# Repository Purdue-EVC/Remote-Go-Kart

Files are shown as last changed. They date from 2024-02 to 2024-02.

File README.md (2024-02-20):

# Rc Go Kart
The Purdue EVC Club's code for the Rc Go kart.
## Setup
Currently using a red line 775 for the steering motor with a SparkMini as the motor controller.
Then using a Rev Robotics Through Bore Encoder for the steering shaft's positioning.
For the brakes we use a linear actuator with a potentiometer as the position sensor.
For motor control we use a sevcon gen4 size 4 with an unknown decade old brushless dc motor.
There is an stm32 controlling the entire kart.
For the remote controller we use a FlySky ia10b receiver with a FlySky i6X for the transmitter.
## Power
Power for all devices except the main motor is entirely from battery power passed through a 48v-12v/5v dc to dc converter. 
12v is supplied to the front steering, braking and the stm32. 5v is supplied to all other devices on the kart.
For the sevcon we use a keyed ignition start along with 2 estops in series connected to the contactor for the sevcon.
Battery power is supplied directly to the sevcon through the contactor.

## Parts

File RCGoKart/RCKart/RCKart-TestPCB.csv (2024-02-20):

Source: | /Users/ryan/Documents/GitHub/EVC-Remote-Cart/RCGoKart/RCKart/RCKart-TestPCB.kicad_sch
Date: | 2023 October 25, Wednesday 09:54:53
Tool: | Eeschema 7.0.7
Generator: | /Applications/KiCad/KiCad.app/Contents/SharedSupport/plugins/bom_csv_grouped_by_value.py
Component Count: | 9
Collated Components:
Item | Qty | Reference(s) | Value | LibPart | Footprint | Datasheet | DNP
1 | 1 | A1 | STM32 Nucleo Board | MCU_Module:Arduino_UNO_R3 | Module:Arduino_UNO_R3_Bare | https://www.arduino.cc/en/Main/arduinoBoardUno
2 | 1 | J1 | Throttle | Connector_Generic:Conn_01x01 | Connector_PinSocket_2.54mm:PinSocket_1x01_P2.54mm_Vertical | ~
3 | 1 | J2 | Brake Controller | Connector_Generic:Conn_01x02 | Connector_PinSocket_2.54mm:PinSocket_1x02_P2.54mm_Vertical | ~
4 | 2 | J3, J13 | RC Channels | Connector_Generic:Conn_01x10 | Connector_PinSocket_2.54mm:PinSocket_1x10_P2.54mm_Vertical | ~
5 | 1 | J6 | Power | Connector:Screw_Terminal_01x03 | TerminalBlock:TerminalBlock_bornier-3_P5.08mm | ~
6 | 1 | J9 | SIG | Connector:Conn_01x04_Socket | Connector_PinSocket_2.54mm:PinSocket_1x04_P2.54mm_Vertical | ~
7 | 1 | J10 | PWR | Connector:Conn_01x04_Socket | Connector_PinSocket_2.54mm:PinSocket_1x04_P2.54mm_Vertical | ~
8 | 1 | J11 | GND | Connector:Conn_01x04_Socket | Connector_PinSocket_2.54mm:PinSocket_1x04_P2.54mm_Vertical | ~

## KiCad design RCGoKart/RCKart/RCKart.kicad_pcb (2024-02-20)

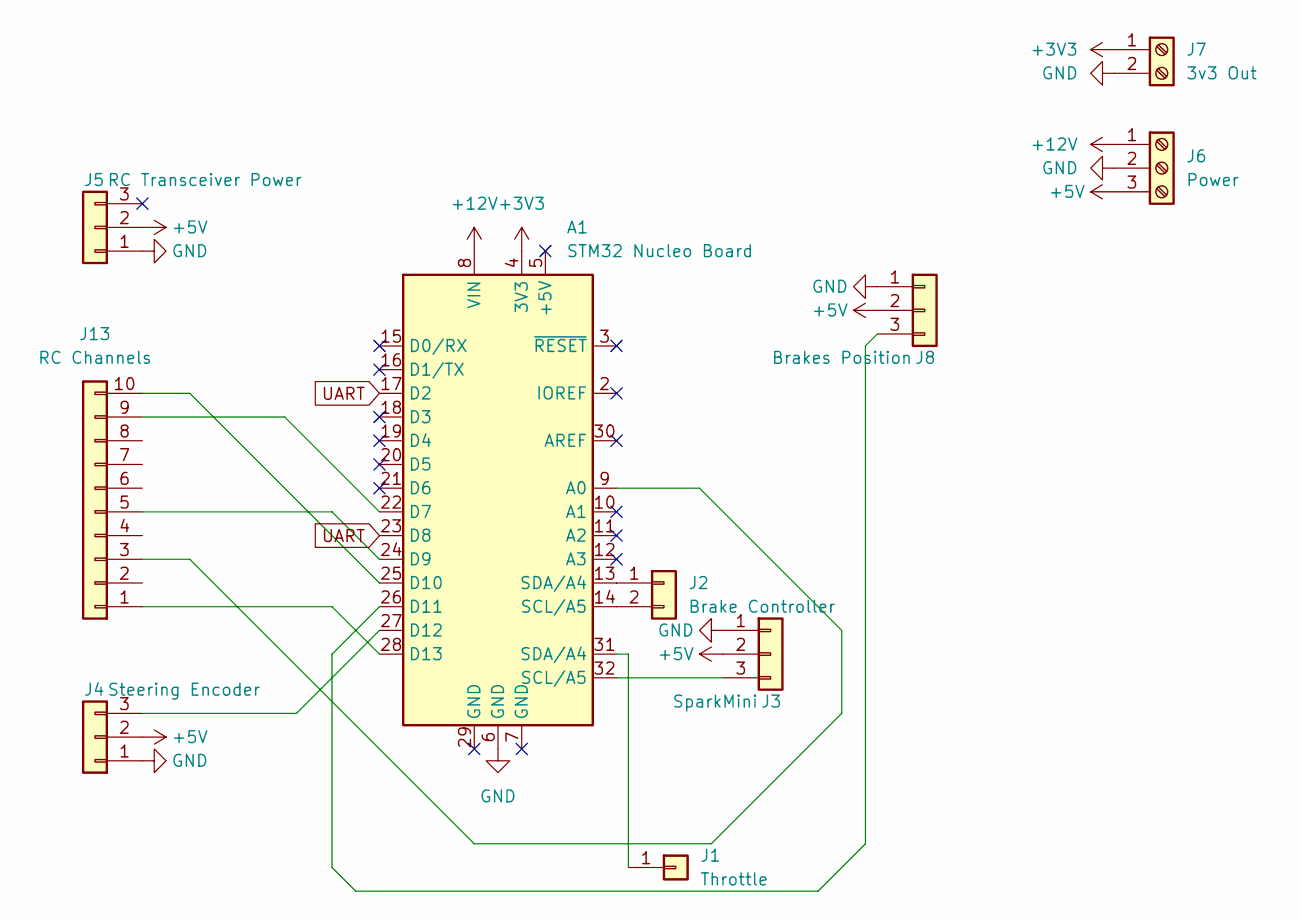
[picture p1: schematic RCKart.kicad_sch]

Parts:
A1: STM32 Nucleo Board; Arduino_UNO_R3_Bare
J1: Throttle; PinSocket_1x01_P2.54mm_Vertical
J2: Brake Controller; PinSocket_1x02_P2.54mm_Vertical
J3: SparkMini; PinHeader_1x03_P2.54mm_Vertical
J4: Steering Encoder; PinHeader_1x03_P2.54mm_Vertical
J5: RC Transceiver Power; PinSocket_1x03_P2.54mm_Vertical
J6: Power; TerminalBlock_bornier-3_P5.08mm
J7: 3v3 Out; TerminalBlock_bornier-2_P5.08mm
J8: Brakes Position; PinSocket_1x03_P2.54mm_Vertical
J13: RC Channels; PinSocket_1x10_P2.54mm_Vertical

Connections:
+3V3: A1.4 (3V3), J7.1
+5V: J3.2, J4.2, J5.2, J6.3, J8.2
+12V: A1.8 (VIN), J6.1
GND: A1.6 (GND), J3.1, J4.1, J5.1, J6.2, J7.2, J8.1
unnamed: A1.9 (A0), J13.3
unnamed: A1.22 (D7), J13.9
unnamed: A1.24 (D9), J13.5
unnamed: A1.25 (D10), J13.10
unnamed: A1.26 (D11), J8.3
unnamed: A1.27 (D12), J4.3
unnamed: A1.28 (D13), J13.1
unnamed: A1.31 (SDA/A4), J1.1
unnamed: A1.13 (SDA/A4), J2.1
unnamed: A1.14 (SCL/A5), J2.2
unnamed: A1.32 (SCL/A5), J3.3
UART: A1.17 (D2), A1.23 (D8)

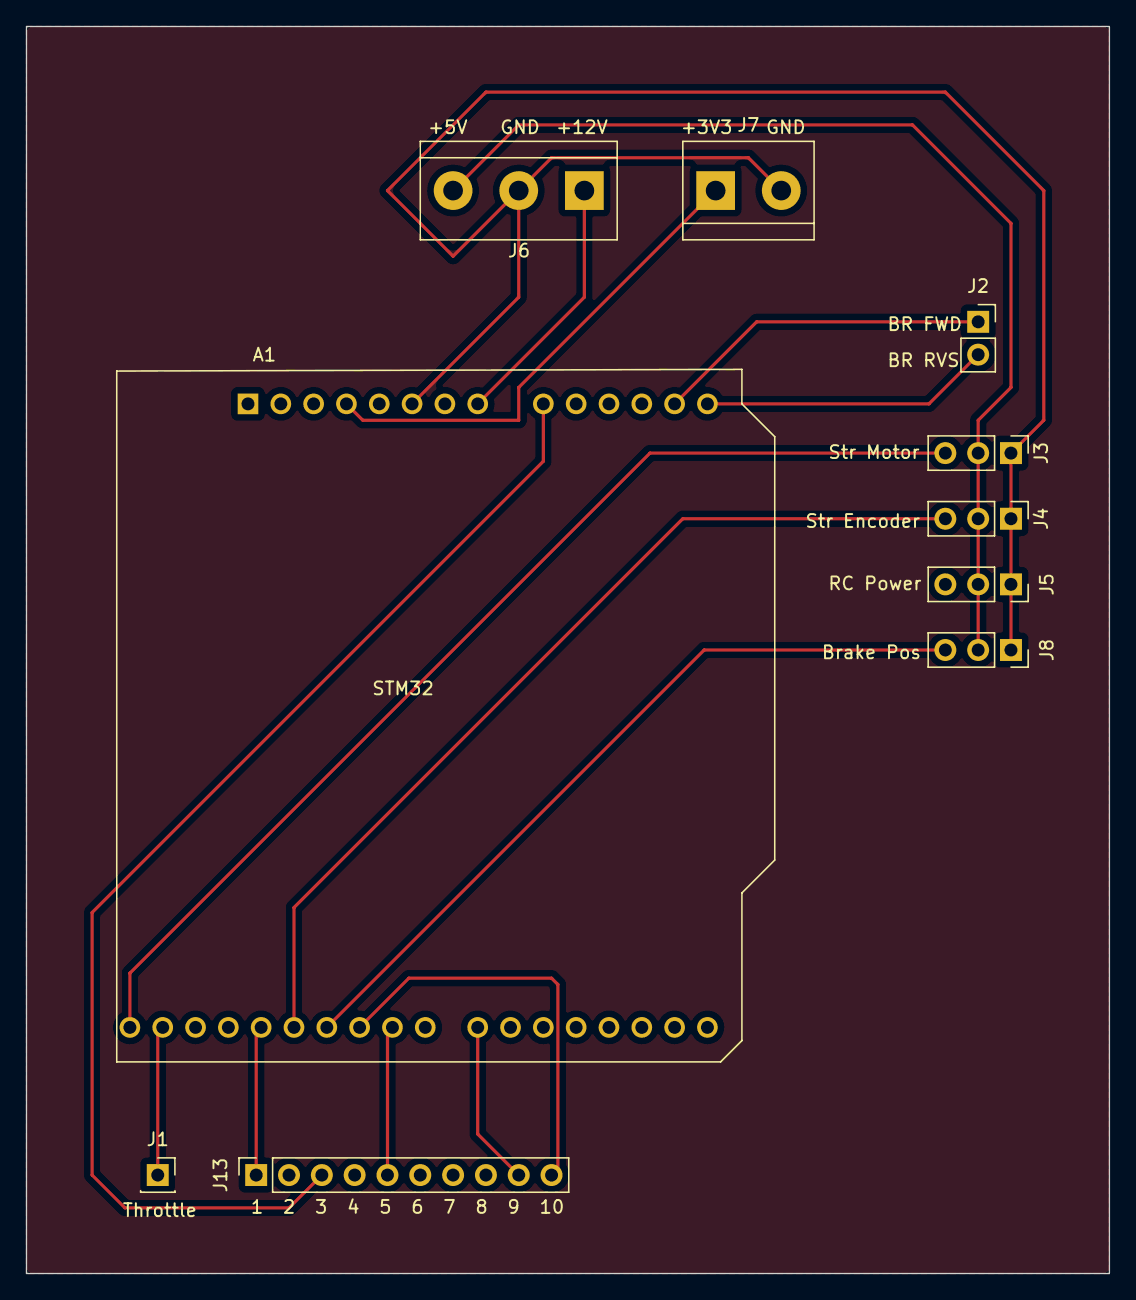
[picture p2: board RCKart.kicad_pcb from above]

Board: 2 copper layers, 83.8 x 96.5 mm, 10 parts (0 on the bottom side), 16 nets.

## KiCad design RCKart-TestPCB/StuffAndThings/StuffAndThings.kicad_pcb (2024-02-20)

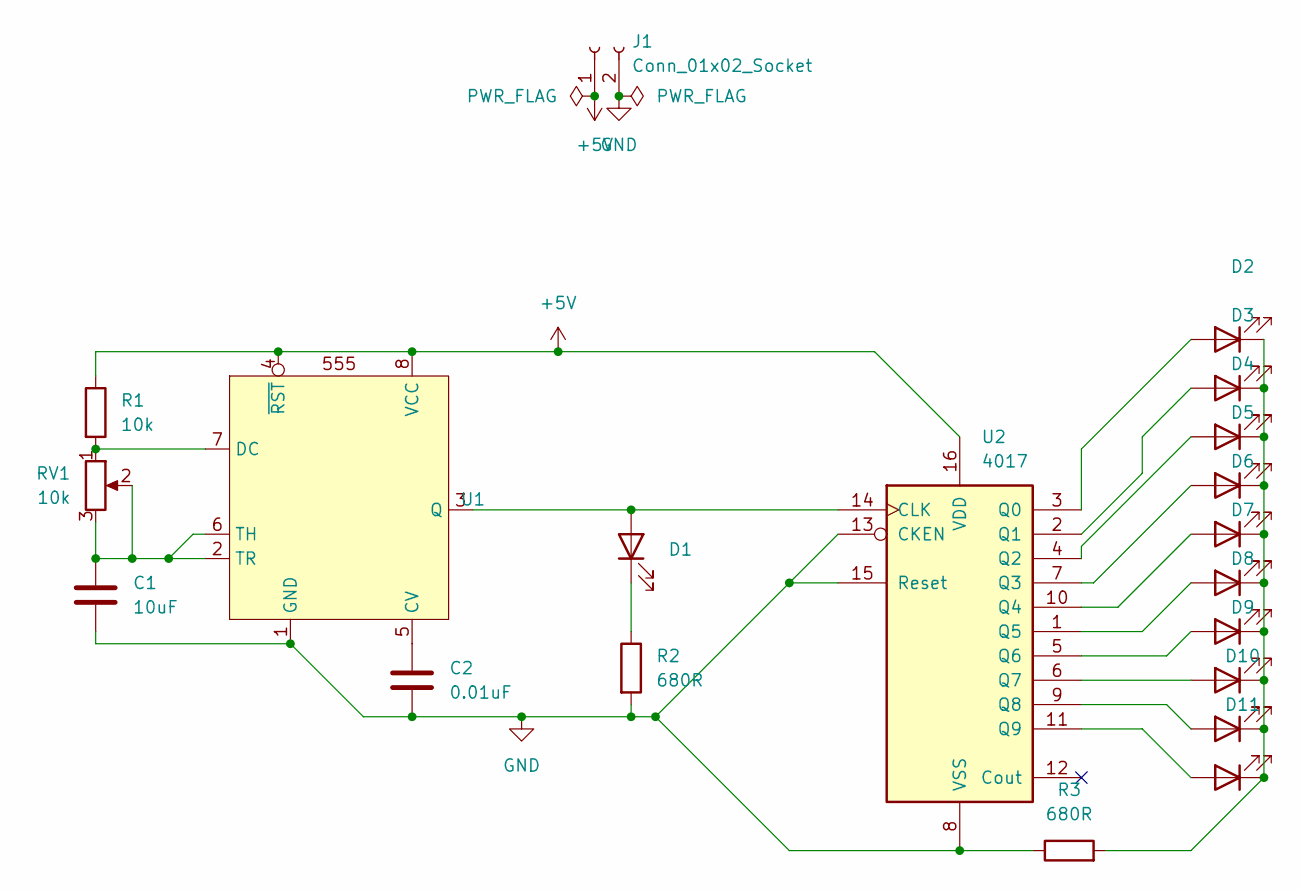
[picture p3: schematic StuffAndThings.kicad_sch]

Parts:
C1: 10uF; C_0402_1005Metric
C2: 0.01uF; C_0402_1005Metric
D1, D2, D3, D4, D5, D6, D7, D8, D9, D10, D11: D_0402_1005Metric
J1: Conn_01x02_Socket; PinSocket_1x02_P2.54mm_Vertical
R1: 10k; R_0402_1005Metric
R2: 680R; R_0603_1608Metric
R3: 680R; R_0402_1005Metric
RV1: 10k; Potentiometer_Bourns_3269P_Horizontal
U1: SOIC-8_3.9x4.9mm_P1.27mm
U2: 4017; SOIC-16_3.9x9.9mm_P1.27mm

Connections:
+5V: J1.1, R1.1, U1.4 (~RST), U1.8 (VCC), U2.16 (VDD)
GND: C1.2, C2.2, J1.2, R2.2, R3.1, U1.1 (GND), U2.8 (VSS), U2.13 (CKEN), U2.15 (Reset)
unnamed: D1.2 (A), U1.3 (Q), U2.14 (CLK)
unnamed: D1.1 (K), R2.1
unnamed: D2.2 (A), U2.3 (Q0)
unnamed: D3.2 (A), U2.2 (Q1)
unnamed: D4.2 (A), U2.4 (Q2)
unnamed: D5.2 (A), U2.7 (Q3)
unnamed: D6.2 (A), U2.10 (Q4)
unnamed: D7.2 (A), U2.1 (Q5)
unnamed: D8.2 (A), U2.5 (Q6)
unnamed: D9.2 (A), U2.6 (Q7)
unnamed: D10.2 (A), U2.9 (Q8)
unnamed: D2.1 (K), D3.1 (K), D4.1 (K), D5.1 (K), D6.1 (K), D7.1 (K), D8.1 (K), D9.1 (K), D10.1 (K), D11.1 (K), R3.2
unnamed: D11.2 (A), U2.11 (Q9)
unnamed: C2.1, U1.5 (CV)
unnamed: R1.2, RV1.1, U1.7 (DC)
unnamed: C1.1, RV1.2, RV1.3, U1.2 (TR), U1.6 (TH)

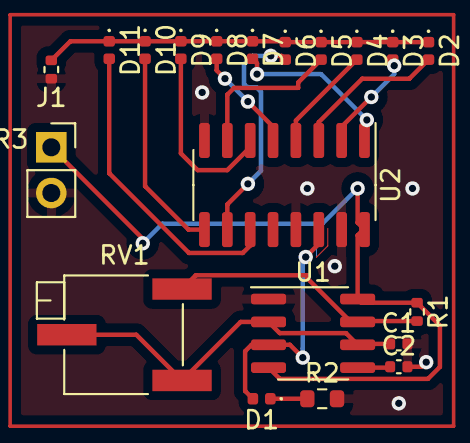
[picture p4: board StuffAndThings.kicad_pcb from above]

Board: 2 copper layers, 20 parts (0 on the bottom side), 18 nets.

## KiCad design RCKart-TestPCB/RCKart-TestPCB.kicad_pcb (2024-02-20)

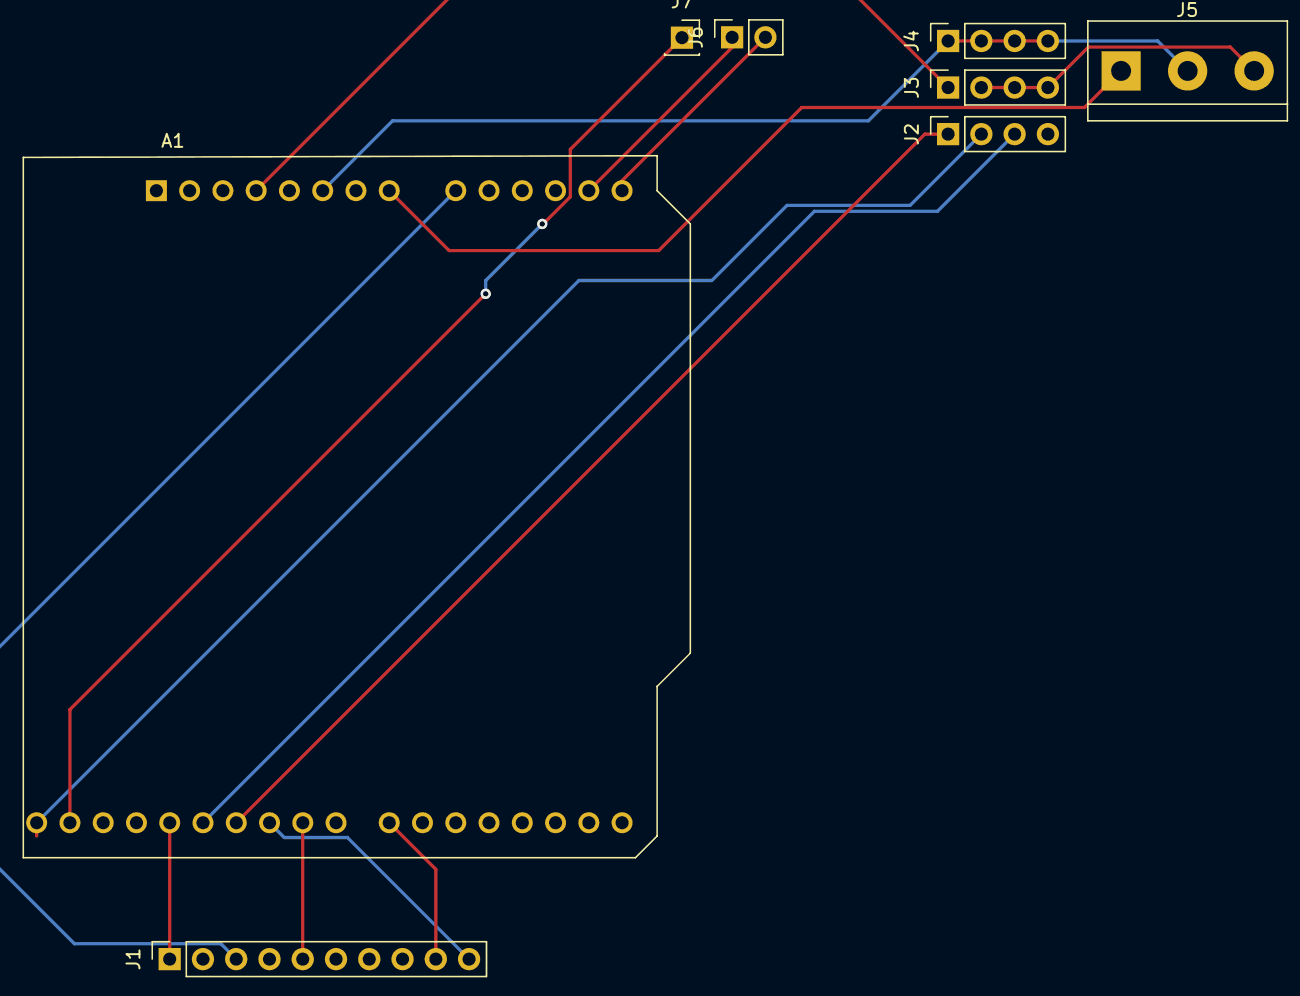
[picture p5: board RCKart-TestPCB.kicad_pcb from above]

Board: 2 copper layers, 8 parts (0 on the bottom side), 15 nets.

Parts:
A1: STM32 Nucleo Board; Arduino_UNO_R3_Bare
J1: RC Channels; PinSocket_1x10_P2.54mm_Vertical
J2: SIG; PinSocket_1x04_P2.54mm_Vertical
J3: PWR; PinSocket_1x04_P2.54mm_Vertical
J4: GND; PinSocket_1x04_P2.54mm_Vertical
J5: Power; TerminalBlock_bornier-3_P5.08mm
J6: Brake Controller; PinSocket_1x02_P2.54mm_Vertical
J7: Throttle; PinSocket_1x01_P2.54mm_Vertical

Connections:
+3V3: A1.4 (3V3), J3.1
+5V: J3.2, J3.3, J3.4, J5.3
+12V: A1.8 (VIN), J5.1
BP: A1.26 (D11), J2.1
ESTOP: A1.25 (D10), J1.10
GND: A1.6 (GND), J4.1, J4.2, J4.3, J4.4, J5.2
MAX SPD: A1.24 (D9), J1.5
unnamed: A1.13 (SDA/A4), J6.1
unnamed: A1.14 (SCL/A5), J6.2
unnamed: A1.31 (SDA/A4), J7.1
SM: A1.32 (SCL/A5), J2.2
STATE: A1.22 (D7), J1.9
STR ENC: A1.27 (D12), J2.3
STR IN: A1.28 (D13), J1.1
THR IN: A1.9 (A0), J1.3

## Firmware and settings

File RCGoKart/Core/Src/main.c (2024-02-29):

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
/* Includes ------------------------------------------------------------------*/
#include "main.h"

/* USER CODE BEGIN Includes */
#include <stdio.h>
#include <stdbool.h>
/* USER CODE END Includes */

/* USER CODE BEGIN PD */

#define PUTCHAR_PROTOTYPE int __io_putchar(int ch)
/* USER CODE END PD */

ADC_HandleTypeDef hadc1;
DMA_HandleTypeDef hdma_adc1;

DAC_HandleTypeDef hdac;

I2C_HandleTypeDef hi2c2;

RTC_HandleTypeDef hrtc;

TIM_HandleTypeDef htim1;
TIM_HandleTypeDef htim2;
TIM_HandleTypeDef htim3;
TIM_HandleTypeDef htim4;
TIM_HandleTypeDef htim5;
TIM_HandleTypeDef htim8;
TIM_HandleTypeDef htim10;
TIM_HandleTypeDef htim11;
TIM_HandleTypeDef htim12;

UART_HandleTypeDef huart2;

/* USER CODE BEGIN PV */

const float kSteeringEncoderMax = 43000.0;
const float kSteeringEncoderMin = 14000.0;
const float kSteeringEncoderRange = 64000.0;

const int maxEncoderAngle = 347;
const int minEncoderAngle = 167;
const int EncoderRange = maxEncoderAngle-minEncoderAngle;//180

const double kOffset = .45;

float kHalDelay = 1;

float maxSpeed = .25;//Range from 0 to 1

//TODO: convert to const once tuned
float kPInverse = 20;
float kP = 0.025;//1/20
float kI = 0.0000001;
float kD = 1;

float error;
float derivative;
float integral = 0;
float pos = 0;
float pastError = 0;
float minError = 0.1;


uint32_t brakePosition = 0;
uint32_t buffer = 0;
/* USER CODE END PV */

void SystemClock_Config(void);
static void MX_GPIO_Init(void);
static void MX_DMA_Init(void);
static void MX_ADC1_Init(void);
static void MX_TIM1_Init(void);
static void MX_TIM2_Init(void);
static void MX_TIM3_Init(void);
static void MX_TIM4_Init(void);
static void MX_TIM5_Init(void);
static void MX_TIM8_Init(void);
static void MX_TIM10_Init(void);
static void MX_TIM11_Init(void);
static void MX_TIM12_Init(void);
static void MX_RTC_Init(void);
static void MX_I2C2_Init(void);
static void MX_USART2_UART_Init(void);
static void MX_DAC_Init(void);
/* USER CODE BEGIN 0 */

uint32_t ICValue = 0;
uint32_t Frequency = 0;
float Duty = 0;
void HAL_TIM_IC_CaptureCallback(TIM_HandleTypeDef *htim)
{
	if (htim->Channel == HAL_TIM_ACTIVE_CHANNEL_1)  // If the interrupt is triggered by channel 1
	{
		// Read the IC value
		ICValue = HAL_TIM_ReadCapturedValue(htim, TIM_CHANNEL_1);

		if (ICValue != 0)
		{
			// calculate the Duty Cycle
			Duty = (HAL_TIM_ReadCapturedValue(htim, TIM_CHANNEL_2) *100)/ICValue;

			Frequency = 90000000/ICValue;
		}
	}
}

float currentSteeringInputMax = 177900;
float currentSteeringInputMin = 90000;
float currentDrivingInputMax = 8935;
float currentDrivingInputMin = 7935;

const float steeringInputAbsoluteMax = 180000;
const float steeringInputAbsoluteMin = 80000;
const float drivingInputAbsoluteMax = 180000;
const float drivingInputAbsoluteMin = 80000;

uint16_t targetBrake = 4095;

float steeringInput(uint32_t rawSteeringInput){
	if(rawSteeringInput > currentSteeringInputMax && rawSteeringInput < steeringInputAbsoluteMax){
		currentSteeringInputMax = rawSteeringInput;
	}
	if(rawSteeringInput < currentSteeringInputMin && rawSteeringInput > steeringInputAbsoluteMin){
		currentSteeringInputMin = rawSteeringInput;
	}
	return (float)(rawSteeringInput-currentSteeringInputMin)/(currentSteeringInputMax-currentSteeringInputMin);
}

float drivingInput(uint32_t rawDrivingInput){
	if(rawDrivingInput > currentDrivingInputMax && rawDrivingInput < drivingInputAbsoluteMax){
		currentDrivingInputMax = rawDrivingInput;
	}
	if(rawDrivingInput < currentDrivingInputMin && rawDrivingInput > drivingInputAbsoluteMin){
		return 0.0;
	}
	return (float)(rawDrivingInput-currentDrivingInputMin)/(currentDrivingInputMax-currentDrivingInputMin);
}


//TODO: Yet to be tested:
float getPIDPower(float currentPosition, float requestPosition, float cycleTime){//New version:
	if(currentPosition<110){
		currentPosition = currentPosition+360;
	}
	error = requestPosition-currentPosition;
	if((error>minError||-minError>error)||(pastError>minError||-minError>pastError)){
		integral = integral + (error * cycleTime);
		derivative = (error-pastError)/cycleTime;
		pastError = error;
		pos = kP*error+kI*integral+kD*derivative+kOffset;
		if(pos>1){
			return 1;
		}
		else if(pos<0){
			return 0;
		}
		else{
			return pos;
		}
	}
	else{
		integral = 0;
		return .5;
	}
}

float getEncoderAngle(){
	return (((int)(36000*((TIM3->CCR2-kSteeringEncoderMin)/(kSteeringEncoderRange)))+18000)%36000)/100;
}

float rawSteeringToAngle(float steerInput){
	return (steerInput*EncoderRange)+minEncoderAngle;
}
float steerout = 0;
float steeroutp = 0;

/**
 * Sets the steering motor's power
 */
void setSteeringMotor(float power){
		steeroutp = power;
		float out = (power)*180.0;//Converts the range 0 to 1, to 90 to 180 //Dont ask why its that range it just works
		steerout = out;
		TIM10->CCR1 = out+45.0;
}
/**
 * Sets the driving motor's power
 */
void setDrivingMotor(float power){
	short int out = (power)*4096;//convert to 3.3v range
	o = out;
	if(power<=0){
		 HAL_DAC_SetValue(&hdac, DAC_CHANNEL_1,
		 DAC_ALIGN_12B_R, 0);//Motor off
	}
	else{
		 HAL_DAC_SetValue(&hdac, DAC_CHANNEL_1,
		 DAC_ALIGN_12B_R, out);//Motor on
	}
}

void setMotor(float power){//0 to 1.0
		 HAL_DAC_SetValue(&hdac, DAC_CHANNEL_1,
		 DAC_ALIGN_12B_R, power);
}

short int bstate = 0;
/**
 * Sets the brake motors power
 */
void setBrakes(){
    HAL_ADC_Start(&hadc1);
    HAL_ADC_PollForConversion(&hadc1, 500);
	brakePosition = HAL_ADC_GetValue(&hadc1);
    HAL_ADC_Stop(&hadc1);
	bstate = 0;
	if(brakePosition+5>targetBrake&&brakePosition-5<targetBrake){
		HAL_GPIO_WritePin(GPIOC, GPIO_PIN_2, GPIO_PIN_RESET);
		HAL_GPIO_WritePin(GPIOC, GPIO_PIN_1, GPIO_PIN_RESET);
		bstate = 2;
	}
	else if(brakePosition>targetBrake){
		HAL_GPIO_WritePin(GPIOC, GPIO_PIN_2, GPIO_PIN_SET);
		HAL_GPIO_WritePin(GPIOC, GPIO_PIN_1, GPIO_PIN_RESET);
		bstate = 0;
	}
	else if(brakePosition<targetBrake-100){
		HAL_GPIO_WritePin(GPIOC, GPIO_PIN_2, GPIO_PIN_RESET);
		HAL_GPIO_WritePin(GPIOC, GPIO_PIN_1, GPIO_PIN_SET);
		bstate = 1;
	}
	else{
		HAL_GPIO_WritePin(GPIOC, GPIO_PIN_2, GPIO_PIN_RESET);
		HAL_GPIO_WritePin(GPIOC, GPIO_PIN_1, GPIO_PIN_RESET);
		bstate = 2;
	}
}

void setBrakeTarget(int request){
	if(request>7935){
		targetBrake = 4095;
	}
	else{
		targetBrake = ((request-5300)*.093)+3850;
	}
	if(targetBrake < 3850){
		targetBrake  = 3850;
	}
}

float tim1 = 0;
float tim2 = 0;
float tim3 = 0;
float tim4 = 0;
float tim5 = 0;
float tim6 = 0;
float tim7 = 0;
float tim8 = 0;
float tim9 = 0;
float tim10 = 0;
float tim11 = 0;
float tim12 = 0;
float a = 0;
float b = 0;
int cycle = 0;
int cycleCount = 5;
uint32_t steeringRequest = (steeringInputAbsoluteMin+steeringInputAbsoluteMax/2);
uint32_t drivingRequest = 0;
/* USER CODE END 0 */

/**
  * @brief  The application entry point.
  * @retval int
  */
int main(void)
{
  /* USER CODE BEGIN 1 */
	hdac.State = HAL_DAC_STATE_RESET;
  /* USER CODE END 1 */

  /* MCU Configuration--------------------------------------------------------*/

  /* Reset of all peripherals, Initializes the Flash interface and the Systick. */
  HAL_Init();

  /* USER CODE BEGIN Init */
  uint16_t pwmBottomState = 5000;
  uint16_t pwmLowState = 25000;
  uint16_t pwmHighState = 45000;
  /* USER CODE END Init */

  /* Configure the system clock */
  SystemClock_Config();

  /* USER CODE BEGIN SysInit */
//  RCC->AHB1ENR |= (1<<0);
  /* USER CODE END SysInit */

  /* Initialize all configured peripherals */
  MX_GPIO_Init();
  MX_DMA_Init();
  MX_ADC1_Init();
  MX_TIM1_Init();
  MX_TIM2_Init();
  MX_TIM3_Init();
  MX_TIM4_Init();
  MX_TIM5_Init();
  MX_TIM8_Init();
  MX_TIM10_Init();
  MX_TIM11_Init();
  MX_TIM12_Init();
  MX_RTC_Init();
  MX_I2C2_Init();
  MX_USART2_UART_Init();
  MX_DAC_Init();
  /* USER CODE BEGIN 2 */
  //Starts HAL timing for input capture
  HAL_TIM_IC_Start_IT(&htim1, TIM_CHANNEL_1);
  HAL_TIM_IC_Start(&htim1, TIM_CHANNEL_2);
  HAL_TIM_IC_Start_IT(&htim2, TIM_CHANNEL_1);
  HAL_TIM_IC_Start(&htim2, TIM_CHANNEL_2);
  HAL_TIM_IC_Start_IT(&htim3, TIM_CHANNEL_1);
  HAL_TIM_IC_Start(&htim3, TIM_CHANNEL_2);
  HAL_TIM_IC_Start_IT(&htim4, TIM_CHANNEL_1);
  HAL_TIM_IC_Start(&htim4, TIM_CHANNEL_2);
  HAL_TIM_IC_Start_IT(&htim5, TIM_CHANNEL_1);
  HAL_TIM_IC_Start(&htim5, TIM_CHANNEL_2);
  HAL_TIM_IC_Start_IT(&htim8, TIM_CHANNEL_1);
  HAL_TIM_IC_Start(&htim8, TIM_CHANNEL_2);
  HAL_TIM_IC_Start_IT(&htim8, TIM_CHANNEL_1);
  HAL_TIM_IC_Start(&htim8, TIM_CHANNEL_2);
  HAL_TIM_IC_Start_IT(&htim12, TIM_CHANNEL_1);
  HAL_TIM_IC_Start(&htim12, TIM_CHANNEL_2);


  HAL_TIM_PWM_Start(&htim10, TIM_CHANNEL_1);
  HAL_TIM_PWM_Start(&htim11, TIM_CHANNEL_1);
  HAL_DAC_Start(&hdac, DAC_CHANNEL_1);
  /* USER CODE END 2 */

  /* Infinite loop */
  /* USER CODE BEGIN WHILE */
  while (1)
  {
    /* USER CODE END WHILE */

    /* USER CODE BEGIN 3 */
	  tim1 = TIM1->CCR2;
	  tim2 = TIM2->CCR2;
	  tim3 = TIM3->CCR2;
	  tim4 = TIM4->CCR2;
	  tim5 = TIM5->CCR2;
	  tim6 = TIM6->CCR2;
	  tim7 = TIM7->CCR2;
	  tim8 = TIM8->CCR2;
	  tim9 = TIM9->CCR2;
	  tim10 = TIM10->CCR1;
	  tim11 = TIM11->CCR1;
	  tim12 = TIM12->CCR2;
	  if(TIM4->CCR2>pwmLowState){//Checking if E-Stop is switched to the high state, forces user on RC controller to switch the e-stop switch to start it
		  //Inputs
		  steeringRequest = tim2;
		  drivingRequest = tim12;
		  b = steeringInput(steeringRequest);
		  //State management
		  if(TIM1->CCR2<pwmBottomState){//Switch to RC mode, middle switch state
			  setSteeringMotor(getPIDPower(getEncoderAngle(), rawSteeringToAngle(b), (float)kHalDelay));
			  setDrivingMotor(drivingInput(drivingRequest));
			  setBrakeTarget(tim12);

		  }
		  else if(TIM1->CCR2>pwmHighState){//Switch to auto mode, high switch state
//			  Manual RC Control
			  setSteeringMotor(b);
			  setDrivingMotor(drivingInput(drivingRequest));
			  setBrakeTarget(tim12);
		  }
		  else{
			  //off state, low switch state
			setMotor(0.0);
			targetBrake = 3850;//Full Brakes
		  }
		  HAL_Delay(1);//For faster response decrease delay
		  setBrakes();
	  }
	  else{
		  //TODO: Debug Relay
			HAL_GPIO_WritePin(GPIOC, GPIO_PIN_2, GPIO_PIN_RESET);
			HAL_GPIO_WritePin(GPIOC, GPIO_PIN_1, GPIO_PIN_RESET);
			setMotor(0.0);
			setSteeringMotor(0.5);
	  }
  }
  /* USER CODE END 3 */
}

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
/* USER CODE BEGIN 4 */



/**
  * @brief  Retargets the C library printf function to the USART.
  * @param  None
  * @retval None
  */
PUTCHAR_PROTOTYPE
{
  /* Place your implementation of fputc here */
  /* e.g. write a character to the USART1 and Loop until the end of transmission */
  HAL_UART_Transmit(&huart2, (uint8_t *)&ch, 1, 0xFFFF);

  return ch;
}
/* USER CODE END 4 */
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


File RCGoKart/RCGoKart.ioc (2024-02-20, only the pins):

Mcu.UserName=STM32F446RETx
PA0-WKUP.Signal=S_TIM5_CH1
PA13.GPIO_Label=TMS
PA13.Signal=SYS_JTMS-SWDIO
PA14.GPIO_Label=TCK
PA14.Signal=SYS_JTCK-SWCLK
PA2.Signal=USART2_TX
PA3.Signal=USART2_RX
PA4.Signal=COMP_DAC1_group
PA5.Signal=S_TIM2_CH1_ETR
PA6.Signal=S_TIM3_CH1
PA7.Signal=ADCx_IN7
PA8.Signal=S_TIM1_CH1
PB10.Signal=I2C2_SCL
PB14.Signal=S_TIM12_CH1
PB3.GPIO_Label=SWO
PB3.Signal=SYS_JTDO-SWO
PB6.Signal=S_TIM4_CH1
PB8.Signal=S_TIM10_CH1
PB9.Signal=S_TIM11_CH1
PC0.Signal=GPIO_Output
PC1.Signal=GPIO_Output
PC12.Signal=I2C2_SDA
PC13.GPIO_Label=B1 [Blue PushButton]
PC13.Signal=GPXTI13
PC14-OSC32_IN.Signal=RCC_OSC32_IN
PC15-OSC32_OUT.Signal=RCC_OSC32_OUT
PC2.Signal=GPIO_Output
PC7.Signal=S_TIM8_CH2
PH0-OSC_IN.Signal=RCC_OSC_IN
PH1-OSC_OUT.Signal=RCC_OSC_OUT

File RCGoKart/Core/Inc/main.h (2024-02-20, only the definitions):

#define B1_Pin GPIO_PIN_13
#define B1_GPIO_Port GPIOC
#define TMS_Pin GPIO_PIN_13
#define TMS_GPIO_Port GPIOA
#define TCK_Pin GPIO_PIN_14
#define TCK_GPIO_Port GPIOA
#define SWO_Pin GPIO_PIN_3
#define SWO_GPIO_Port GPIOB

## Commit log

2023-09-01 Create TalonTestSpeedController.ino
    This code should be able to control the talon srx as if it is a servo with max servo angle as max speed and min angle as off
2023-09-02 Create jsTestDebug.js
    Used to test pid programming
2023-09-18 Uploaded Current STM32 Code
2023-09-18 fixed simple code mismatches
    [main.c]
2023-09-18 Added ConvertPWMInToOut
    converts the pwm in from the rc stick to pwm out for the steering motor
2023-09-18 Uploaded Current Code
2023-09-18 Fixed Uart
2023-09-18 Updated TIM to correct channels
    [main.c]
2023-09-26 wip pid and motor control functions
2023-10-03 WIP Schematics
    [RCKart.kicad_pcb, RCKart.kicad_sch]
2023-10-03 Fixed % error and attempted fix for UART
    Uart switched to huart2, rawSteeringToAngle now has .01 accuracy and is a float
    [RCGoKart.ioc, main.c]
2023-10-04 Added DAC, New PID, Fixed Motor Control
    DAC is used to control the motor as it is an analog not a pwm signal. New PID loop has been implemented and read to test, it removes the max angle of the motor by using the P the proper way and limiting power output rather than positional output.
    [main.c]
2023-10-05 Working Code Uploaded, PID testing needed
    PID is last thing to test. Motor needs to be debugged but it seems to not be a mcu error.
    [RCKart.kicad_sch]
2023-10-09 Brakes Implemented
2023-10-24 WIP PCB
    [RCKart-B_Cu.gbr, RCKart-B_Mask.gbr, RCKart-B_Paste.gbr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]
2023-10-25 Added Test PCB Wiring
    [RCKart-TestPCB.csv, RCKart-TestPCB.kicad_pcb, RCKart-TestPCB.kicad_sch]
2023-10-26 Test PCB work
    [RCKart-TestPCB.kicad_pcb]
2024-02-20 Added Braking, reimplemented all working code for testing
    Braking currently works on pin a4 and a3. Currently steering is ready as well, however gearbox issues are still a wip for the steering motor, after fixes slop may decrease. Driving has not changed since the last implementation, it will need to change input stick at some point however that will happen once the rest of the kart is ready.
    Todo:
    Implement and fix estop relay
    Setup failsafe on controller for kart
    Finish mount for the batteries
    Fix and remount steering motor
    [StuffAndThings.kicad_pcb, StuffAndThings.kicad_sch]
2024-02-29 Updated Driving Motor Code
    Code is ready to test on rc kart

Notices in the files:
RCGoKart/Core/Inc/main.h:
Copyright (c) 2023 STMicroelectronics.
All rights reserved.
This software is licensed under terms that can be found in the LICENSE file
